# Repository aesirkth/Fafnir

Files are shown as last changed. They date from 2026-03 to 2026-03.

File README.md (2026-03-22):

# Fafnir
Propulsion Engine Controller

# Prerequisites
Follow [zephyr getting started guide](https://docs.zephyrproject.org/latest/develop/getting_started/index.html)

# Build 

```bash
cd zephyr-firmware
west update
cd fafnir
west build -b fafnir app --pristine
west flash
```

# Build for native simulation
```bash
docker run -ti -v /Volumes/external/zephyrproject/:/workdir -v /Volumes/external/aesir/Fafnir/zephyr-firmware/:/app ghcr.io/zephyrproject-rtos/zephyr-build:main
cd /app/fafnir
west build -b native_sim/native/64 app --pristine -- -DEXTRA_CONF_FILE=debug.conf
./build/zephyr/zephyr.exe
```
or
```bash
west build -b native_sim/native/64 app -- -DEXTRA_CONF_FILE=debug.conf && ./build/zephyr/zephyr.exe
```

## Using shell in simulation

You can send can messages like this
```bash
uart: ~$ can send can_loopback0 ID DATA
```

For example, running
```bash
uart: ~$ can send can_loopback0 123 0
```
will tell Fafnir to go into state STATE_INIT.

Running 
```bash
uart: ~$ can send can_loopback0 124 0 1
```
will use the override feature to set N2 Valve HIGH.

# CAN message specification to Fafnir

| CAN ID | byte | data | type  |
| --- | ---- | --- | ----- |
| 0x123  | 0 | launch sequence number (1-6) | uint8 | (setting states mode)
| 0x124  | 0 | Solenoid ID (1-4) | uint8 | (override mode)
| | 1 | 1 == open, 0 == closed | bool  |

Note that the launch sequence number corresponds to the launch sequence number as given in https://aesir.slab.com/posts/mjollnir-launch-sequence-2juh5ekp

Note that the Solenoid ID corresponds to the solenoid ports on the Fafnir board.
Mjollnir only has two solenoids which correspond to:
```
Solenoid ID 2 => Bypass valve
Solenoid ID 3 => Pilot valve
Solenoid ID 4 => Control vent
```
Solenoid IDs 1 and 4 are not connected and don't do anything.

## CAN acknowledges

| CAN ID | byte | data | meaning |
| --- | ---- | ---  | -----|
| 0x125  | 0 | 0x01 | Changing state! |
| | 1 |  \<byte\> |  the state we're changing to |
| 0x125  | 0 | 0x02 | Received valid override command! |
| | 1 | \<byte\> | The first byte we received  |
| | 2 |  \<byte\> | The second byte we received  |
| 0x125  | 0 | 0xF0 | Recieved invalid state |
| 0x125  | 0 | 0xF1 | Cannot perform ignition command while attempting ignition. (Protection against double send) |
|  | 1 | \<byte\> | State command we received |
| 0x125  | 0 | 0xF2 | Invalid state command |
| 0x125  | 0 | 0xF3 | Invalid override command |
| 0x125  | 0 | 0xF4 | Invalid pin given in override command |

The state we're changing to is of type equal to this C `enum`:
```c
typedef enum {
    STATE_IDLE,
    STATE_INIT,
    STATE_FILL,
    STATE_STOP_FILL,
    STATE_UMBILICAL,
    STATE_N2_PRESSURIZATION,
    STATE_IGNITION_1,
    STATE_IGNITION_2,
    STATE_IGNITION_3,
    STATE_IGNITION_4,
    STATE_SAFE,
    STATE_ABORT_BEFORE_COUNTDOWN,
    STATE_ABORT_AFTER_COUNTDOWN
} State_t;
```

Note that this is **NOT** the same as the launch sequence number used in the command above (0x123).

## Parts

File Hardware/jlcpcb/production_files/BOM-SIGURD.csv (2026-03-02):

Comment | Designator | Footprint | LCSC | Quantity
54.9k | R18 | R_0402_1005Metric | C11626 | 1
1k | R23,R24,R27,R28,R42 | R_0402_1005Metric | C11702 | 5
100p | C39 | C_0402_1005Metric | C1546 | 1
18p | C10,C9 | C_0402_1005Metric | C1549 | 2
47p | C26 | C_0402_1005Metric | C1567 | 1
30p | C34 | C_0402_1005Metric | C1570 | 1
1u | C38 | C_0603_1608Metric | C15849 | 1
10u | C29,C31,C43 | C_0805_2012Metric | C15850 | 3
3.9u | L1 | L_Changjiang_FNR4030S | C167872 | 1
49.9k | R17 | C_0402_1005Metric | C173335 | 1
3V | D10,D11,D14,D16,D18 | D_SOD-323 | C19077437 | 5
LED | D7 | D_0603_1608Metric | C19171301 | 1
10u | C13,C22,C41,C42 | C_0603_1608Metric | C194427 | 4
CSD17577Q3A | Q3 | VSON-8_3.3x3.3mm_P0.65mm_NexFET | C201632 | 1
MMBT3904 | Q1 | SOT-23 | C20526 | 1
1.0A | F10,F11,F7,F8,F9 | Fuse_1812_4532Metric | C20997 | 5
1k | R22,R4,R5 | R_0603_1608Metric | C21190 | 3
TPS56A37RPAR | IC3 | RPA0010A-MFG | C22392669 | 1
52.3k | R47 | R_0402_1005Metric | C227130 | 1
120 | R10 | R_0603_1608Metric_Pad0.98x0.95mm_HandSolder | C22787 | 1
rx | D4 | D_0603_1608Metric | C2286 | 1
LED | D9 | D_0603_1608Metric | C2288 | 1
LED | D21,D3 | D_0603_1608Metric | C2290 | 2
1M | R12,R13,R14,R15 | R_0603_1608Metric | C22935 | 4
3k | R30,R39 | R_0603_1608Metric | C22978 | 2
SZNUP2105L | D6 | SOT-23 | C23083861 | 1
470 | R2 | R_0603_1608Metric_Pad0.98x0.95mm_HandSolder | C23179 | 1
D | D2 | D_SOD-523 | C232841 | 1
4.7u | C1,C11,C2,C28 | C_0402_1005Metric | C23733 | 4
100 | R50 | R_0402_1005Metric | C25076 | 1
10 | R25,R51 | R_0402_1005Metric | C25077 | 2
120 | R52 | R_0402_1005Metric | C25079 | 1
10k | R11,R16,R20,R35,R45,R9 | R_0402_1005Metric | C25744 | 6
15k | R19,R46 | R_0402_1005Metric | C25756 | 2
20k | R49 | R_0402_1005Metric | C25765 | 1
10k | R3 | R_0603_1608Metric_Pad0.98x0.95mm_HandSolder | C25804 | 1
3.3k | R7,R8 | R_0402_1005Metric | C25890 | 2
INA226 | U4 | VSSOP-10_3x3mm_P0.5mm | C2653870 | 1
TCAN334GDCN | U1 | TSOT-23-8 | C2671013 | 1
ESD2CAN36DBZRQ1 | CR1,CR2 | SOT-23-3_DBZ_TEX | C284078 | 2
0.1u | C14,C15,C17,C19,C23,C27,C3,C30,C32,C35,C4,C40,C44,C5,C6,C7,C8 | C_0402_1005Metric | C307331 | 17
47k | R29,R31,R32,R33,R34,R36,R37,R38,R43,R44 | R_0603_1608Metric | C307918 | 10
~ | D12,D13,D15,D17,D19 | D_0603_1608Metric | C328933 | 5
24MHz | Y1 | Crystal_SMD_2016-4Pin_2.0x1.6mm | C37635323 | 1
~ | D1 | D_SOD-123 | C435489 | 1
7.5k | R26 | R_0603_1608Metric | C441926 | 1
VN7050ASTR | U7 | SOIC_050ASTR_STM | C443993 | 1
22u | C36,C37 | C_0805_2012Metric | C45783 | 2
383k | R48 | R_0402_1005Metric | C45993 | 1
TPS4H160AQPWPRQ1 | U6 | PWP0028C_N | C485918 | 1
0.02 | R21,R6 | R_2512_6332Metric | C49164694 | 2
10u | L2 | IND-SMD_L7.0-W6.6_FAUL06XX | C5298253 | 1
5.6u | L3 | IND-SMD_L6.6-W6.4 | C5378545 | 1
330n | C24 | C_0402_1005Metric | C5448882 | 1
22u | C16,C21 | C_0603_1608Metric | C59461 | 2
LM51231QRGRRQ1 | U3 | RGR0020C-MFG | C6286802 | 1
470p | C12 | C_0402_1005Metric | C76971 | 1
AP63203WU | U9 | TSOT-23-6 | C780769 | 1
CSD18543Q3A | Q4 | VSON-8_3.3x3.3mm_P0.65mm_NexFET | C840100 | 1
0.47u | C33 | C_0402_1005Metric | C92361 | 1
6.8n | C25 | C_0402_1005Metric | C93654 | 1
CMT-8504-100 | BZ1 | BUZ-SMD_4P-L7.5-W7.5-P7.59-TL | C95299 | 1
LED | D20 | D_0603_1608Metric | C965807 | 1

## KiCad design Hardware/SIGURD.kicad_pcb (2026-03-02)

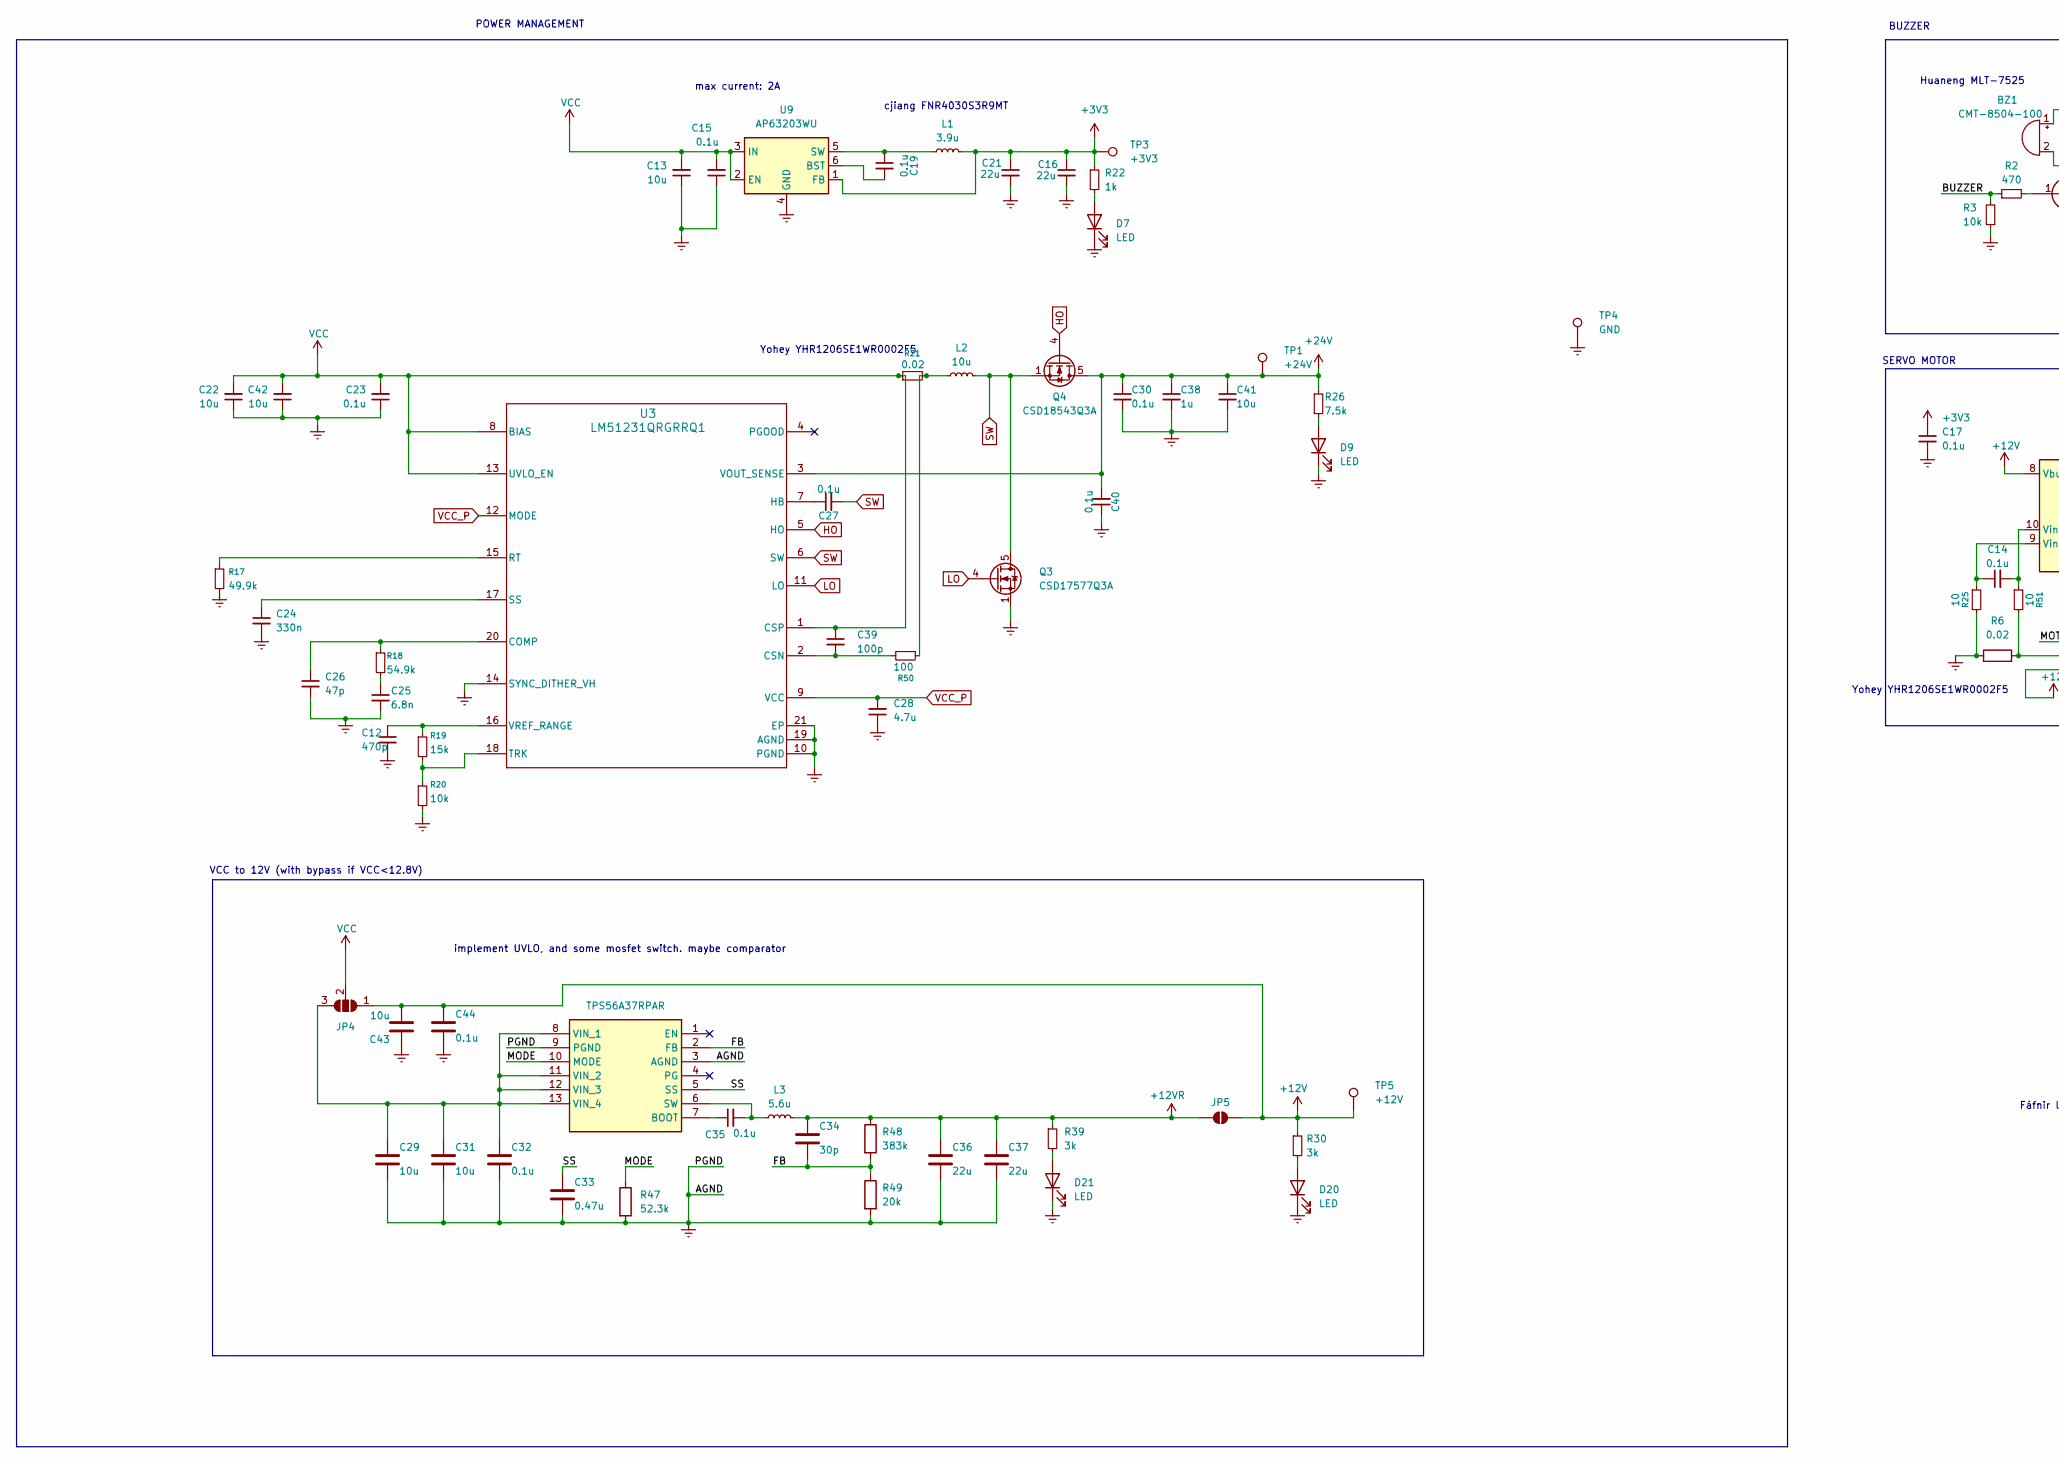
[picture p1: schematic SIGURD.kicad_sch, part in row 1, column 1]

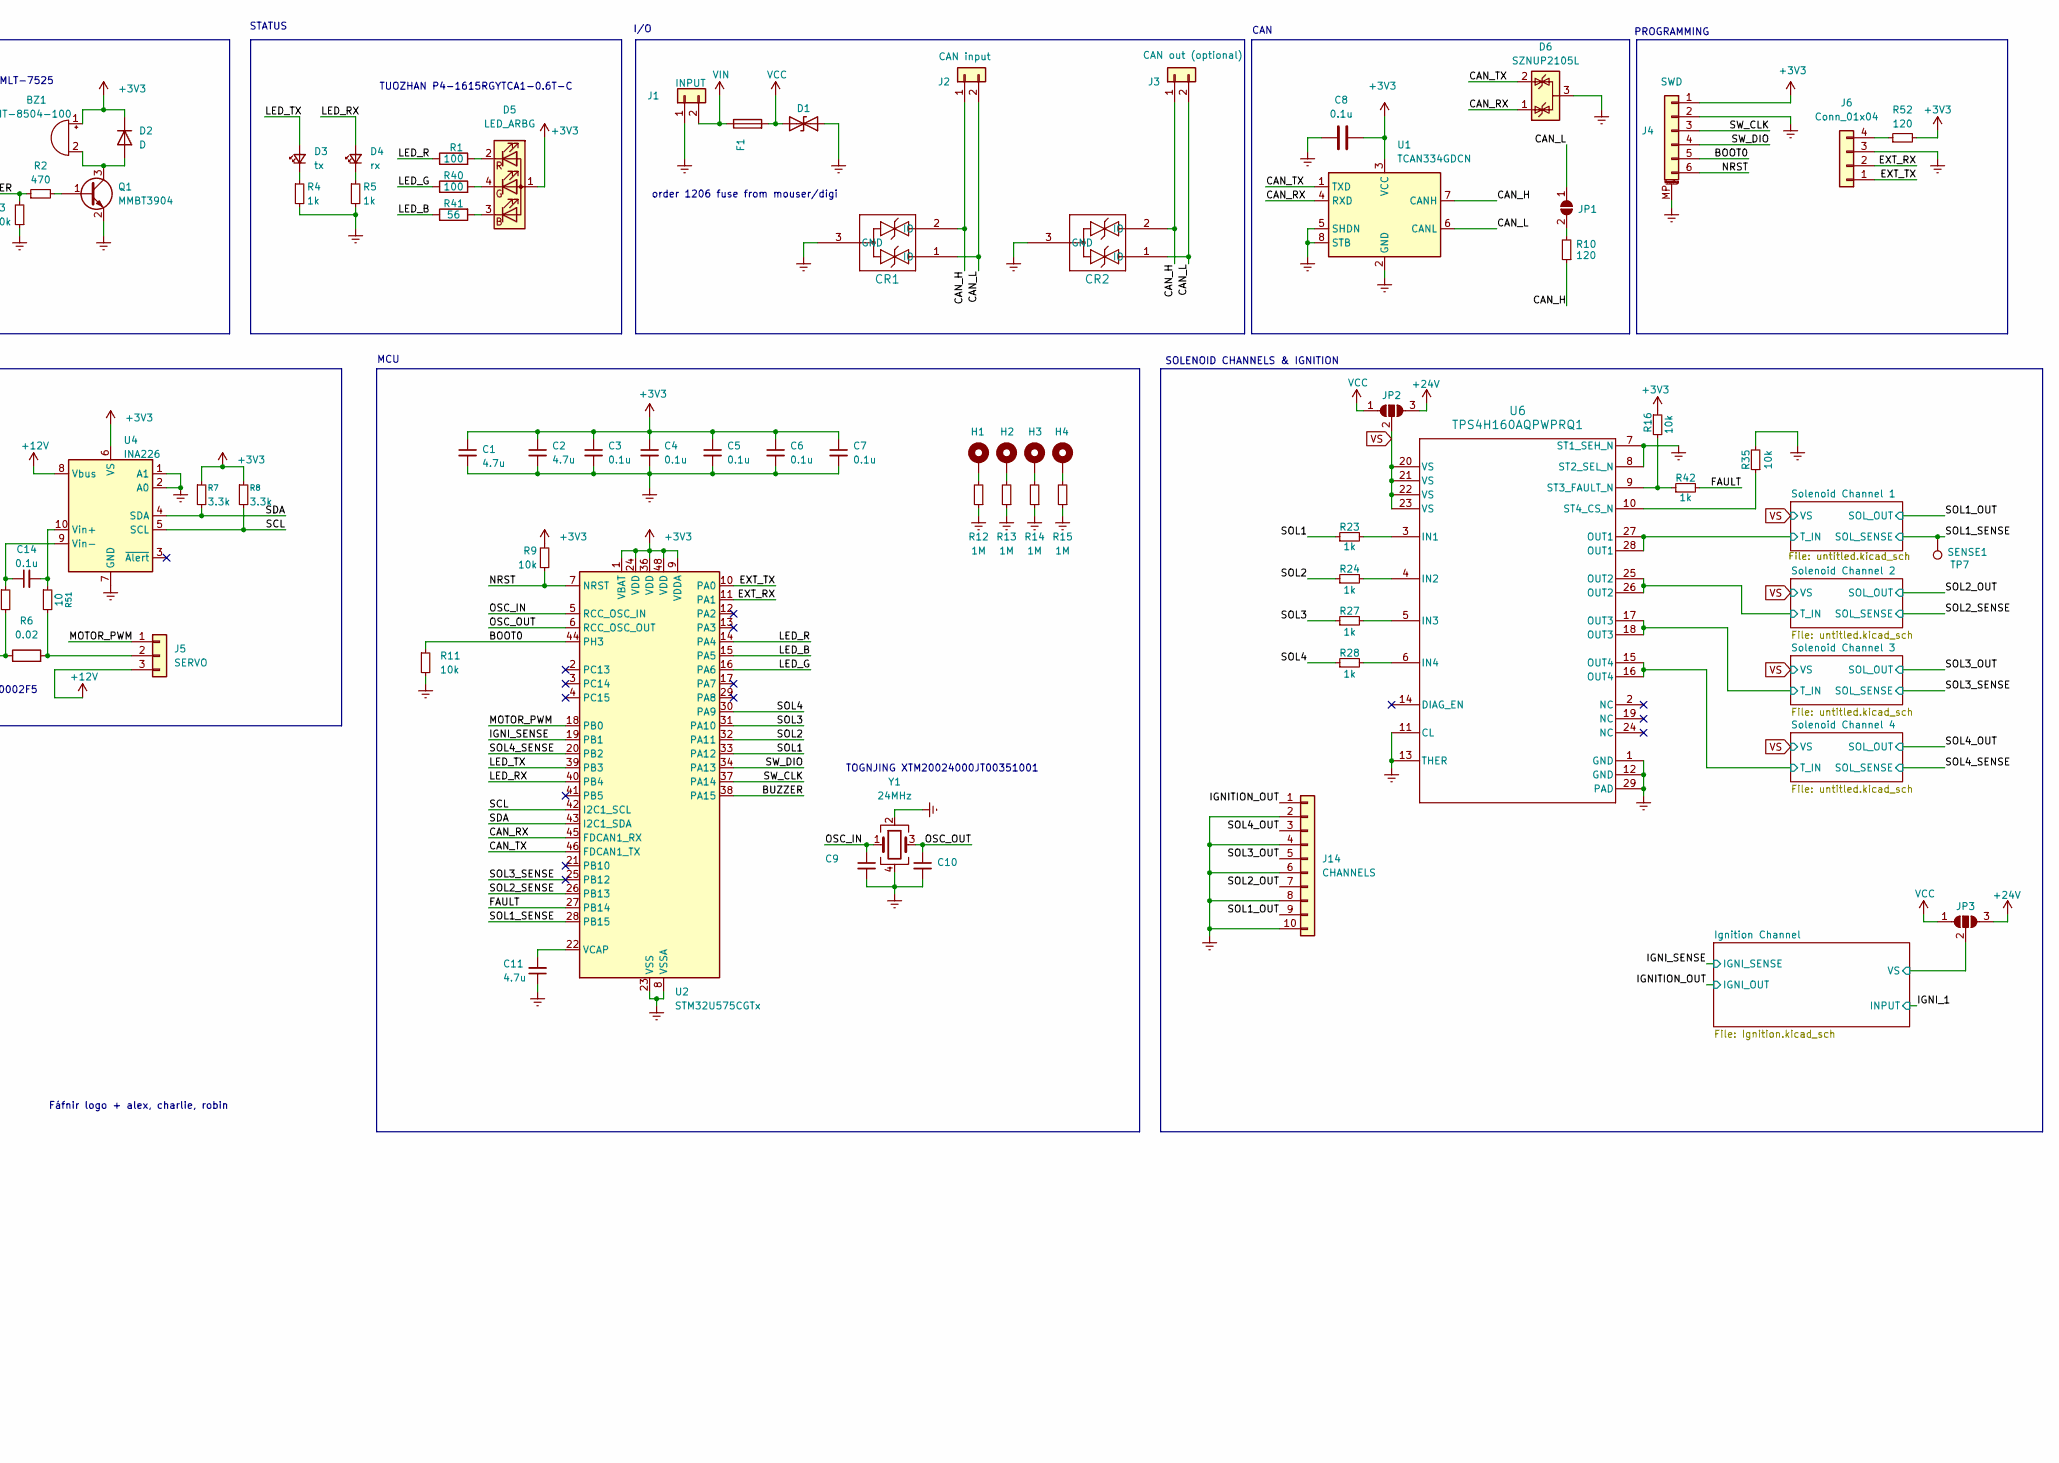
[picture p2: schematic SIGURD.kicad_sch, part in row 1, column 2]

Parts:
BZ1: CMT-8504-100; BUZ-SMD_4P-L7.5-W7.5-P7.59-TL
C1, C2, C11, C28: 4.7u; C_0402_1005Metric
C3, C4, C5, C6, C7, C8, C14, C15, C17, C19, C23, C27, C30, C32, C35, C40, C44: 0.1u; C_0402_1005Metric
C9, C10: 18p; C_0402_1005Metric
C12: 470p; C_0402_1005Metric
C13, C22, C41, C42: 10u; C_0603_1608Metric
C16, C21: 22u; C_0603_1608Metric
C24: 330n; C_0402_1005Metric
C25: 6.8n; C_0402_1005Metric
C26: 47p; C_0402_1005Metric
C29, C31, C43: 10u; C_0805_2012Metric
C33: 0.47u; C_0402_1005Metric
C34: 30p; C_0402_1005Metric
C36, C37: 22u; C_0805_2012Metric
C38: 1u; C_0603_1608Metric
C39: 100p; C_0402_1005Metric
CR1, CR2: ESD2CAN36DBZRQ1; SOT-23-3_DBZ_TEX
D1: D_SOD-123
D2: D; D_SOD-523
D3: tx; D_0603_1608Metric
D4: rx; D_0603_1608Metric
D5: LED_ARBG; LED_Lumex_SML-LX0404SIUPGUSB
D6: SZNUP2105L; SOT-23
D7, D9, D20, D21: LED; D_0603_1608Metric
F1: 15A; Fuse_1206_3216Metric
H1, H2, H3, H4: MountingHole_Pad; MountingHole_3.2mm_M3_Pad_Via
IC3: TPS56A37RPAR; RPA0010A-MFG; Mouser Part Number 595-TPS56A37RPAR
J1: INPUT; AMASS_XT30PW-F_1x02_P2.50mm_Horizontal
J2: CAN input; JST_XH_B2B-XH-A_1x02_P2.50mm_Vertical
J3: CAN out (optional); JST_XH_B2B-XH-A_1x02_P2.50mm_Vertical
J4: SWD; JST_SH_SM06B-SRSS-TB_1x06-1MP_P1.00mm_Horizontal
J5: SERVO; CONN_1727023_PXC
J6: Conn_01x04; PinSocket_1x04_P1.27mm_Vertical
J14: CHANNELS; CONN10_1935242_PXC
JP1: SolderJumper_2_Open; SolderJumper-2_P1.3mm_Open_TrianglePad1.0x1.5mm
JP2, JP3: SolderJumper_3_Open; SolderJumper-3_P2.0mm_Open_TrianglePad1.0x1.5mm_NumberLabels
JP4: SolderJumper_3_Open; SolderJumper-3_P1.3mm_Open_Pad1.0x1.5mm_NumberLabels
JP5: SolderJumper_2_Open; SolderJumper-2_P1.3mm_Open_Pad1.0x1.5mm
L1: 3.9u; L_Changjiang_FNR4030S
L2: 10u; IND-SMD_L7.0-W6.6_FAUL06XX
L3: 5.6u; IND-SMD_L6.6-W6.4
Q1: MMBT3904; SOT-23
Q3: CSD17577Q3A; VSON-8_3.3x3.3mm_P0.65mm_NexFET
Q4: CSD18543Q3A; VSON-8_3.3x3.3mm_P0.65mm_NexFET
R1, R40, R50: 100; R_0402_1005Metric
R2: 470; R_0603_1608Metric_Pad0.98x0.95mm_HandSolder
R3: 10k; R_0603_1608Metric_Pad0.98x0.95mm_HandSolder
R4, R5, R22: 1k; R_0603_1608Metric
R6, R21: 0.02; R_2512_6332Metric
R7, R8: 3.3k; R_0402_1005Metric
R9, R11, R16, R20, R35: 10k; R_0402_1005Metric
R10: 120; R_0603_1608Metric_Pad0.98x0.95mm_HandSolder
R12, R13, R14, R15: 1M; R_0603_1608Metric
R17: 49.9k; C_0402_1005Metric
R18: 54.9k; R_0402_1005Metric
R19: 15k; R_0402_1005Metric
R23, R24, R27, R28, R42: 1k; R_0402_1005Metric
R25, R51: 10; R_0402_1005Metric
R26: 7.5k; R_0603_1608Metric
R30, R39: 3k; R_0603_1608Metric
R41: 56; R_0402_1005Metric
R47: 52.3k; R_0402_1005Metric
R48: 383k; R_0402_1005Metric
R49: 20k; R_0402_1005Metric
R52: 120; R_0402_1005Metric
TP1: +24V; TestPoint_Pad_D2.0mm
TP3: +3V3; TestPoint_Pad_D2.0mm
TP4: GND; TestPoint_Pad_D2.0mm
TP5: +12V; TestPoint_Pad_D2.0mm
TP7: SENSE1; TestPoint_Pad_D2.0mm
U1: TCAN334GDCN; TSOT-23-8
U2: STM32U575CGTx; LQFP-48_7x7mm_P0.5mm
U3: LM51231QRGRRQ1; RGR0020C-MFG
U4: INA226; VSSOP-10_3x3mm_P0.5mm
U6: TPS4H160AQPWPRQ1; PWP0028C_N
U9: AP63203WU; TSOT-23-6
Y1: 24MHz; Crystal_SMD_2016-4Pin_2.0x1.6mm

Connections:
+3V3: BZ1.1 (-), C1.1, C2.1, C3.1, C4.1, C5.1, C6.1, C7.1, C8.2, C16.1, C17.1, C21.1, D2.1 (K), D5.1 (A), J4.1, L1.2, R7.1, R8.1, R9.2, R16.1, R22.1, R52.2, TP3.1, U1.3 (VCC), U2.1 (VBAT), U2.9 (VDDA), U2.24 (VDD), U2.36 (VDD), U2.48 (VDD), U4.6 (VS), U9.1 (FB)
+12V: C43.1, C44.2, J5.3, JP4.1 (A), JP5.2 (B), R30.1, TP5.1, U4.8 (Vbus)
+12VR: C34.2, C36.2, C37.2, JP5.1 (A), L3.2, R39.1, R48.1
+24V: C30.1, C38.1, C40.2, C41.1, JP2.3 (B), JP3.3 (B), Q4.5 (D), R26.1, TP1.1, U3.3 (VOUT_SENSE)
/BOOT0: J4.5, R11.1, U2.44 (PH3)
/BUZZER: R2.1, R3.2, U2.38 (PA15)
/CAN_H: CR1.2 (IO), CR2.2 (IO), J2.1, J3.1, R10.1, U1.7 (CANH)
/CAN_L: CR1.1 (IO), CR2.1 (IO), J2.2, J3.2, JP1.1 (A), U1.6 (CANL)
/CAN_RX: D6.1 (K), U1.4 (RXD), U2.45 (FDCAN1_RX)
/CAN_TX: D6.2 (K), U1.1 (TXD), U2.46 (FDCAN1_TX)
/EXT_RX: J6.2, U2.11 (PA1)
/EXT_TX: J6.1, U2.10 (PA0)
/FAULT: R42.2, U2.27 (PB14)
/FB: C34.1, IC3.2 (FB), R48.2, R49.1
/IGNITION_OUT: J14.1; also elsewhere on the board
/IGNI_SENSE: U2.19 (PB1); also elsewhere on the board
/Ignition Channel/VS: JP3.2 (C); also elsewhere on the board
/LED_B: R41.1, U2.15 (PA5)
/LED_G: R40.1, U2.16 (PA6)
/LED_R: R1.1, U2.14 (PA4)
/LED_RX: D4.2 (A), U2.40 (PB4)
/LED_TX: D3.2 (A), U2.39 (PB3)
/MODE: IC3.10 (MODE), R47.1
/MOTOR_PWM: J5.1, U2.18 (PB0)
/NRST: J4.6, R9.1, U2.7 (NRST)
/OSC_IN: C9.1, U2.5 (RCC_OSC_IN), Y1.1
/OSC_OUT: C10.1, U2.6 (RCC_OSC_OUT), Y1.3
/SCL: R8.2, U2.42 (I2C1_SCL), U4.5 (SCL)
/SDA: R7.2, U2.43 (I2C1_SDA), U4.4 (SDA)
/SOL1: R23.1, U2.33 (PA12)
/SOL1_OUT: J14.9; also elsewhere on the board
/SOL1_SENSE: TP7.1, U2.28 (PB15); also elsewhere on the board
/SOL2: R24.1, U2.32 (PA11)
/SOL2_OUT: J14.7; also elsewhere on the board
/SOL2_SENSE: U2.26 (PB13); also elsewhere on the board
/SOL3: R27.1, U2.31 (PA10)
/SOL3_OUT: J14.5; also elsewhere on the board
/SOL3_SENSE: U2.25 (PB12); also elsewhere on the board
/SOL4: R28.1, U2.30 (PA9)
/SOL4_OUT: J14.3; also elsewhere on the board
/SOL4_SENSE: U2.20 (PB2); also elsewhere on the board
/SS: C33.2, IC3.5 (SS)
/SW_CLK: J4.3, U2.37 (PA14)
/SW_DIO: J4.4, U2.34 (PA13)
/Solenoid Channel 1/T_IN: U6.27 (OUT1), U6.28 (OUT1); also elsewhere on the board
/Solenoid Channel 2/T_IN: U6.25 (OUT2), U6.26 (OUT2); also elsewhere on the board
/Solenoid Channel 3/T_IN: U6.17 (OUT3), U6.18 (OUT3); also elsewhere on the board
/Solenoid Channel 4/T_IN: U6.15 (OUT4), U6.16 (OUT4); also elsewhere on the board
Earth: C1.2, C2.2, C3.2, C4.2, C5.2, C6.2, C7.2, C8.1, C9.2, C10.2, C11.1, C12.2, C13.1, C15.1, C16.2, C17.2, C21.2, C22.1, C23.1, C24.2, C25.2, C26.2, C28.1, C29.1, C30.2, C31.1, C32.1, C33.1, C36.1, C37.1, C38.2, C40.1, C41.2, C42.1, C43.2, C44.1, CR1.3 (GND), CR2.3 (GND), D1.1 (A1), D6.3 (A), D7.1 (K), D9.1 (K), D20.1 (K), D21.1 (K), IC3.3 (AGND), IC3.9 (PGND), J1.1, J4.2, J4.MP (MountPin), J6.3, J14.2, J14.4, J14.6, J14.8, J14.10, Q1.2 (E), Q3.1 (S), Q3.2 (S), Q3.3 (S), R3.1, R4.2, R5.2, R6.1, R11.2, R12.1, R13.1, R14.1, R15.1, R17.2, R20.2, R25.2, R35.2, R47.2, R49.2, TP4.1, U1.2 (GND), U1.5 (SHDN), U1.8 (STB), U2.8 (VSSA), U2.23 (VSS), U2.35 (VSS), U2.47 (VSS), U3.10 (PGND), U3.14 (SYNC_DITHER_VH), U3.19 (AGND), U3.21 (EP), U3.22, U3.23, U3.24, U3.25, U3.26, U4.1 (A1), U4.2 (A0), U4.7 (GND), U6.1 (GND), U6.7 (ST1_SEH_N), U6.8 (ST2_SEL_N), U6.11 (CL), U6.12 (GND), U6.13 (THER), U6.29 (PAD), U6.V, U9.4 (GND), Y1.2, Y1.4; also elsewhere on the board
HO: Q4.4 (G), U3.5 (HO)
LO: Q3.4 (G), U3.11 (LO)
unnamed: BZ1.2 (+), D2.2 (A), Q1.3 (C)
unnamed: C25.1, R18.2
unnamed: D3.1 (K), R4.1
unnamed: D4.1 (K), R5.1
unnamed: D5.3 (BK), R41.2
unnamed: D5.4 (GK), R40.2
unnamed: D5.2 (RK), R1.2
unnamed: D7.2 (A), R22.2
unnamed: D9.2 (A), R26.2
unnamed: D20.2 (A), R30.2
unnamed: D21.2 (A), R39.2
unnamed: H1.1, R12.2
unnamed: H2.1, R13.2
unnamed: H3.1, R14.2
unnamed: H4.1, R15.2
unnamed: C35.1, IC3.7 (BOOT)
unnamed: C35.2, IC3.6 (SW), L3.1
unnamed: C29.2, C31.2, C32.2, IC3.8 (VIN_1), IC3.11 (VIN_2), IC3.12 (VIN_3), IC3.13 (VIN_4), JP4.3 (B)
unnamed: J5.2, R6.2, R51.2
unnamed: J6.4, R52.1
unnamed: JP1.2 (B), R10.2
unnamed: L2.1, R21.2, R50.1
unnamed: Q1.1 (B), R2.2
unnamed: C11.2, U2.22 (VCAP)
unnamed: C26.1, R18.1, U3.20 (COMP)
unnamed: C39.2, R50.2, U3.2 (CSN)
unnamed: C27.1, U3.7 (HB)
unnamed: R17.1, U3.15 (RT)
unnamed: C24.1, U3.17 (SS)
unnamed: R19.2, R20.1, U3.18 (TRK)
unnamed: C12.1, R19.1, U3.16 (VREF_RANGE)
unnamed: C14.2, R51.1, U4.10 (Vin+)
unnamed: C14.1, R25.1, U4.9 (Vin-)
unnamed: R23.2, U6.3 (IN1)
unnamed: R24.2, U6.4 (IN2)
unnamed: R27.2, U6.5 (IN3)
unnamed: R28.2, U6.6 (IN4)
unnamed: R16.2, R42.1, U6.9 (ST3_FAULT_N)
unnamed: R35.1, U6.10 (ST4_CS_N)
unnamed: C19.2, U9.6 (BST)
unnamed: C19.1, L1.1, U9.5 (SW)
SW: C27.2, L2.2, Q3.5 (D), Q4.1 (S), Q4.2 (S), Q4.3 (S), U3.6 (SW)
VCC: C13.2, C15.2, C22.2, C23.2, C39.1, C42.2, D1.2 (A2), F1.2, JP2.1 (A), JP3.1 (A), JP4.2 (C), R21.1, U3.1 (CSP), U3.8 (BIAS), U3.13 (UVLO_EN), U9.2 (EN), U9.3 (IN)
VCC_P: C28.2, U3.9 (VCC), U3.12 (MODE)
VIN: F1.1, J1.2
VS: JP2.2 (C), U6.20 (VS), U6.21 (VS), U6.22 (VS), U6.23 (VS); also elsewhere on the board

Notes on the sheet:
BUZZER
VCC to 12V (with bypass if VCC<12.8V)
I/O
SOLENOID CHANNELS & IGNITION
Yohey YHR1206SE1WR0002F5
Huaneng MLT-7525
Fáfnir logo + alex, charlie, robin
PROGRAMMING
cjiang FNR4030S3R9MT
max current: 2A
implement UVLO, and some mosfet switch. maybe comparator
order 1206 fuse from mouser/digi
CAN
POWER MANAGEMENT
TOGNJING XTM20024000JT00351001
SERVO MOTOR
TUOZHAN P4-1615RGYTCA1-0.6T-C
MCU
STATUS

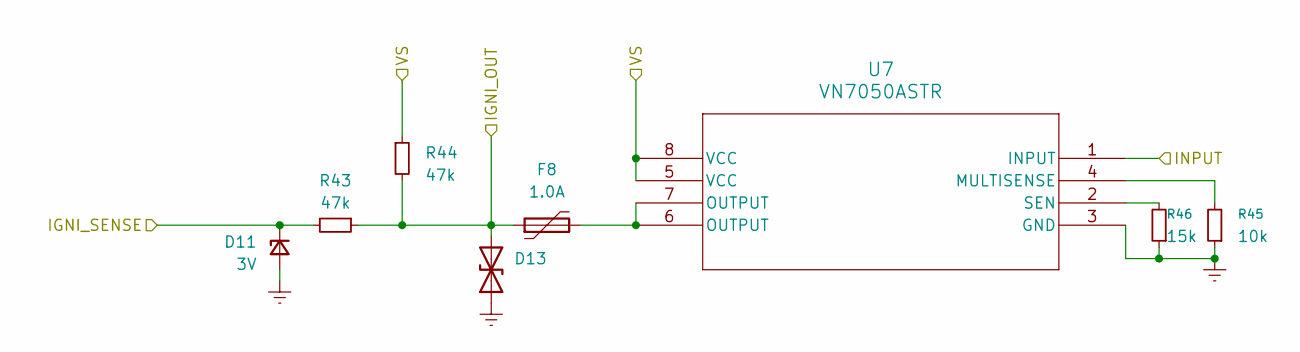
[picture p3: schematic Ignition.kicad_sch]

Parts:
D11: 3V; D_SOD-323
D13: D_0603_1608Metric
F8: 1.0A; Fuse_1812_4532Metric
R43, R44: 47k; R_0603_1608Metric
R45: 10k; R_0402_1005Metric
R46: 15k; R_0402_1005Metric
U7: VN7050ASTR; SOIC_050ASTR_STM

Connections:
/IGNITION_OUT: D13.2 (A2), F8.1, R43.1, R44.2; also elsewhere on the board
/IGNI_1: U7.1 (INPUT)
/IGNI_SENSE: D11.1 (K), R43.2; also elsewhere on the board
/Ignition Channel/VS: R44.1, U7.5 (VCC), U7.8 (VCC); also elsewhere on the board
Earth: D11.2 (A), D13.1 (A1), R45.1, R46.1, U7.3 (GND); also elsewhere on the board
unnamed: F8.2, U7.6 (OUTPUT), U7.7 (OUTPUT)
unnamed: R45.2, U7.4 (MULTISENSE)
unnamed: R46.2, U7.2 (SEN)

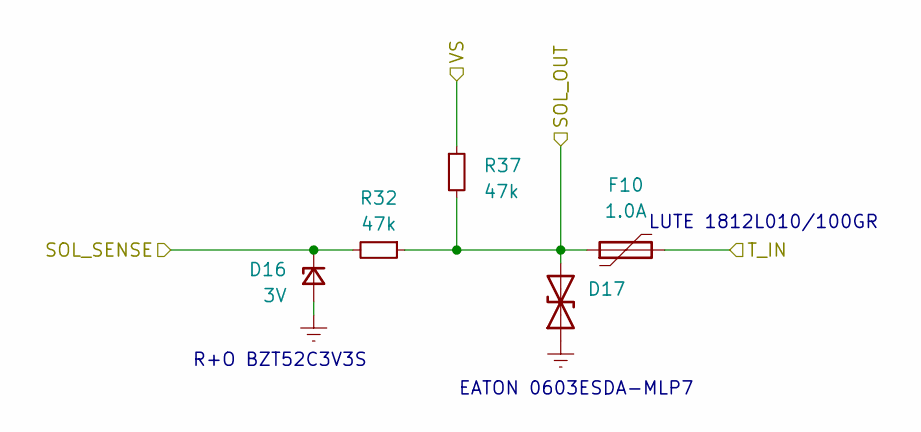
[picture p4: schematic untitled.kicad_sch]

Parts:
D16: 3V; D_SOD-323
D17: D_0603_1608Metric
F10: 1.0A; Fuse_1812_4532Metric
R32, R37: 47k; R_0603_1608Metric

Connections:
/SOL3_OUT: D17.2 (A2), F10.1, R32.1, R37.2; also elsewhere on the board
/SOL3_SENSE: D16.1 (K), R32.2; also elsewhere on the board
/Solenoid Channel 3/T_IN: F10.2; also elsewhere on the board
Earth: D16.2 (A), D17.1 (A1); also elsewhere on the board
VS: R37.1; also elsewhere on the board

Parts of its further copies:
D10, D14, D18: 3V; D_SOD-323
D12, D15, D19: D_0603_1608Metric
F7, F9, F11: 1.0A; Fuse_1812_4532Metric
R29, R31, R33, R34, R36, R38: 47k; R_0603_1608Metric

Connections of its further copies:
/SOL1_OUT: D12.2 (A2), F7.1, R29.1, R34.2; also elsewhere on the board
/SOL1_SENSE: D10.1 (K), R29.2; also elsewhere on the board
/SOL2_OUT: D15.2 (A2), F9.1, R31.1, R36.2; also elsewhere on the board
/SOL2_SENSE: D14.1 (K), R31.2; also elsewhere on the board
/SOL4_OUT: D19.2 (A2), F11.1, R33.1, R38.2; also elsewhere on the board
/SOL4_SENSE: D18.1 (K), R33.2; also elsewhere on the board
/Solenoid Channel 1/T_IN: F7.2; also elsewhere on the board
/Solenoid Channel 2/T_IN: F9.2; also elsewhere on the board
/Solenoid Channel 4/T_IN: F11.2; also elsewhere on the board
Earth: D10.2 (A), D12.1 (A1), D14.2 (A), D15.1 (A1), D18.2 (A), D19.1 (A1); also elsewhere on the board
VS: R34.1, R36.1, R38.1; also elsewhere on the board

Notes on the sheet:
R+O BZT52C3V3S
LUTE 1812L010/100GR
EATON 0603ESDA-MLP7

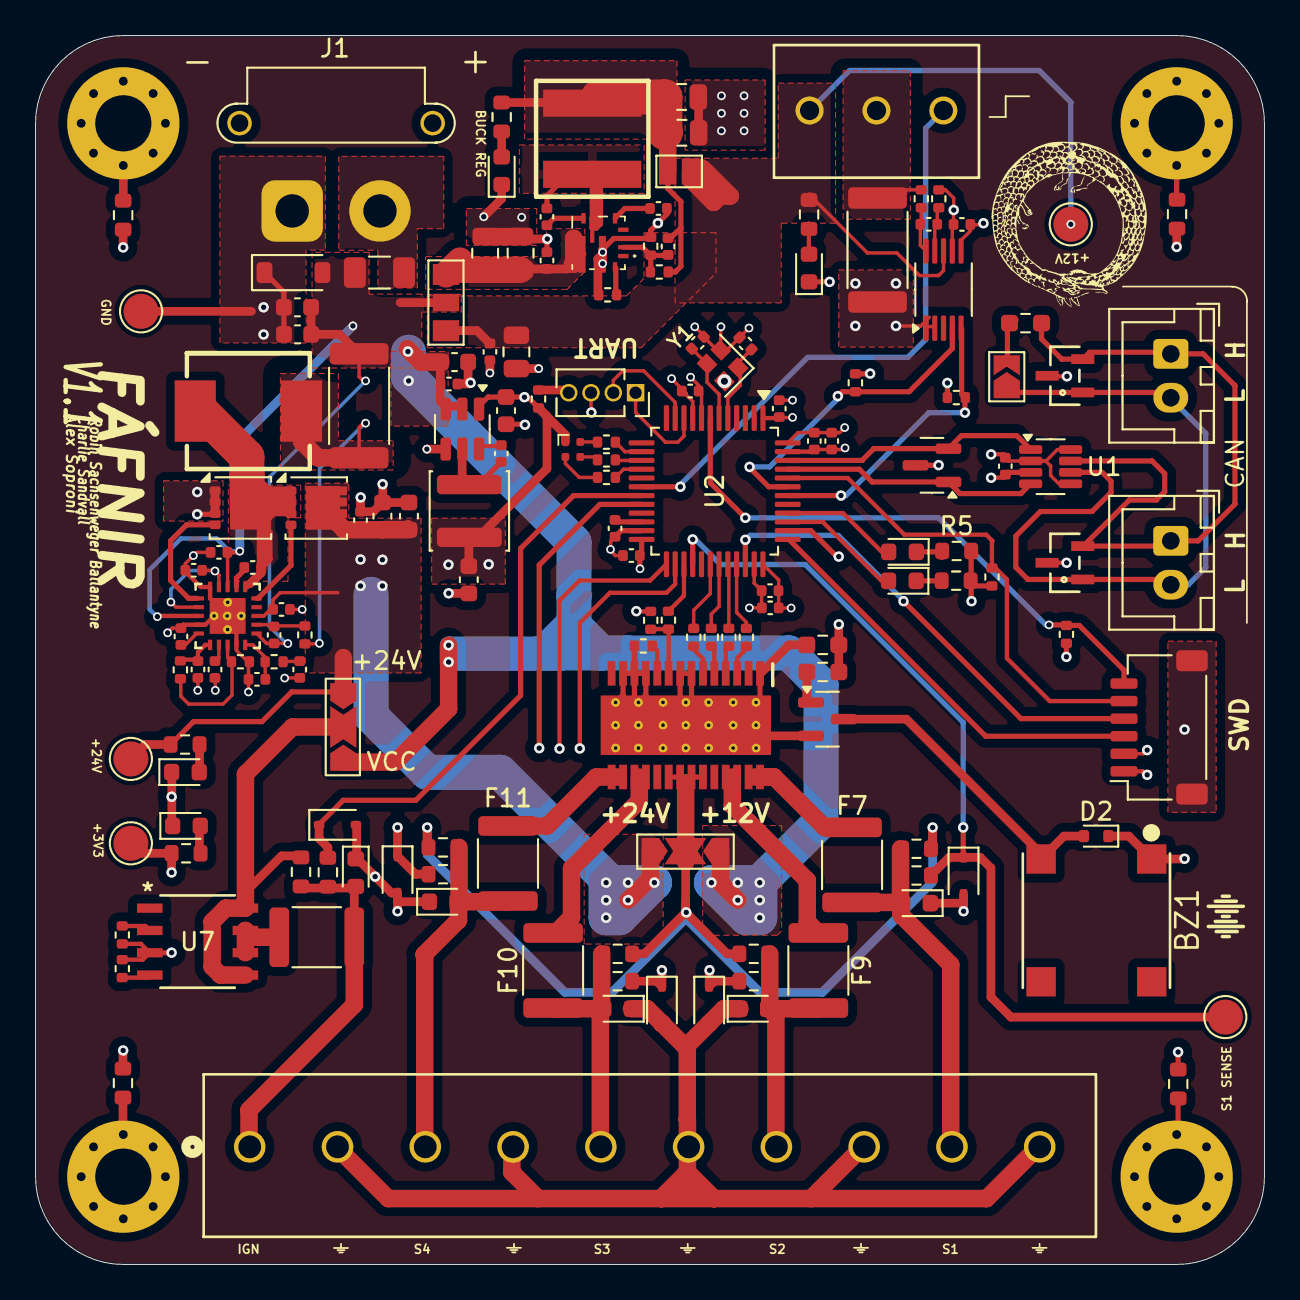
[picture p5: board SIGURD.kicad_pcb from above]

Board: 4 copper layers, 70.0 x 70.0 mm, 159 parts (0 on the bottom side), 100 nets.

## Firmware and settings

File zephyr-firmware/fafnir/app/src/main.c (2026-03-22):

/*
 * Copyright (c) 2016 Intel Corporation
 *
 * SPDX-License-Identifier: Apache-2.0
 */

#include "can_com.h"

#if defined(CONFIG_BOARD_NATIVE_SIM) 
#include "gpio_emul_shell.h"
#endif

#include "main.h"

#include <zephyr/logging/log.h>
#include <zephyr/kernel.h>
#include <zephyr/drivers/gpio.h>
#include <zephyr/drivers/pwm.h>



/* 1000 msec = 1 sec */
#define SLEEP_TIME_MS   4000


LOG_MODULE_REGISTER(main_func);

static const struct gpio_dt_spec led = GPIO_DT_SPEC_GET(DT_ALIAS(rxled), gpios);

// Disable servo pwm if using board Native Sim 
// #if !defined(CONFIG_BOARD_NATIVE_SIM) 
// static const struct pwm_dt_spec pwm_servo = PWM_DT_SPEC_GET(DT_NODELABEL(servo));
// #define SERVO_PERIOD PWM_MSEC(20)
// #endif

#if !defined(CONFIG_BOARD_NATIVE_SIM) 
static const struct pwm_dt_spec pwm_servo = PWM_DT_SPEC_GET(DT_ALIAS(servo));
#define SERVO_PERIOD PWM_MSEC(20)
#endif

static const struct gpio_dt_spec N2_valve = GPIO_DT_SPEC_GET(DT_ALIAS(n2valve), gpios);
static const struct gpio_dt_spec vent_valve = GPIO_DT_SPEC_GET(DT_ALIAS(ventvalve), gpios);
static const struct gpio_dt_spec abort_valve = GPIO_DT_SPEC_GET(DT_ALIAS(abortvalve), gpios);
static const struct gpio_dt_spec extra_valve = GPIO_DT_SPEC_GET(DT_ALIAS(extravalve), gpios);

// static const struct gpio_dt_spec N2_sense = GPIO_DT_SPEC_GET(DT_ALIAS(n2sense), gpios);
// static const struct gpio_dt_spec vent_sense = GPIO_DT_SPEC_GET(DT_ALIAS(ventsense), gpios);
// static const struct gpio_dt_spec main_sense = GPIO_DT_SPEC_GET(DT_ALIAS(mainsense), gpios);
// static const struct gpio_dt_spec abort_sense = GPIO_DT_SPEC_GET(DT_ALIAS(abortsense), gpios);
// static const struct gpio_dt_spec ignition_sense = GPIO_DT_SPEC_GET(DT_ALIAS(ignitionsense), gpios);

#define NUM_CHANNELS 4
// const struct gpio_dt_spec solenoidSense[NUM_CHANNELS] = {N2_sense, vent_sense, abort_sense, ignition_sense};
const struct gpio_dt_spec pyroPins[NUM_CHANNELS] = {N2_valve, vent_valve, abort_valve, extra_valve};


typedef enum {
    STATE_IDLE,
    STATE_INIT,
    STATE_FILL,
    STATE_STOP_FILL,
    STATE_UMBILICAL,
    STATE_N2_PRESSURIZATION,
    STATE_IGNITION_1,
    STATE_IGNITION_2,
    STATE_IGNITION_3,
    STATE_IGNITION_4,
    STATE_SAFE,
    STATE_ABORT_BEFORE_COUNTDOWN,
    STATE_ABORT_AFTER_COUNTDOWN
} State_t;

State_t systemState = STATE_IDLE;
bool trigger = true;

bool isStateBeforeCountdown(State_t state) {
    switch (state) {
    case STATE_IDLE:
        return true;
    case STATE_INIT:
        return true;
    case STATE_FILL:
        return true;
    case STATE_STOP_FILL:
        return true;
    case STATE_UMBILICAL:
        return true;
    case STATE_N2_PRESSURIZATION:
        return true;
    case STATE_IGNITION_1:
        return true;
    case STATE_IGNITION_2:
        return true;
    case STATE_IGNITION_3:
        return false; // Double checked with xiao
    case STATE_IGNITION_4:
        return false;
    case STATE_SAFE:
        return false;
    case STATE_ABORT_BEFORE_COUNTDOWN:
        return false;
    case STATE_ABORT_AFTER_COUNTDOWN:
        return false;
    }
    LOG_ERR("Invalid state passed!");
    return true;
}

bool isStateIgnition(State_t state) {
    switch (state) {
    case STATE_IDLE:
        return false;
    case STATE_INIT:
        return false;
    case STATE_FILL:
        return false;
    case STATE_STOP_FILL:
        return false;
    case STATE_UMBILICAL:
        return false;
    case STATE_N2_PRESSURIZATION:
        return false;
    case STATE_IGNITION_1:
        return true;
    case STATE_IGNITION_2:
        return true;
    case STATE_IGNITION_3:
        return true;
    case STATE_IGNITION_4:
        return true;
    case STATE_SAFE:
        return false;
    case STATE_ABORT_BEFORE_COUNTDOWN:
        return false;
    case STATE_ABORT_AFTER_COUNTDOWN:
        return false;
    }
    LOG_ERR("Invalid state passed!");
    return false;
}


/* 
 * A CAN message with `data`, is interpreted as a command meaning:
 * "Change your state to `state_can_id_map[data]`".
*/
State_t state_can_id_map[] = {
    STATE_INIT,
    STATE_FILL,
    STATE_STOP_FILL,
    STATE_UMBILICAL,
    STATE_N2_PRESSURIZATION,
    STATE_IGNITION_1,
    STATE_SAFE,
    STATE_ABORT_BEFORE_COUNTDOWN // Used for any abort message, not just before countdown.
};

void changeStateToIgnition2_cb() { 
    if(systemState != STATE_IGNITION_1) return;

    systemState = STATE_IGNITION_2;
    LOG_INF("changeStateToIgnition2_cb triggered going into STATE_IGNITION_2!");
    trigger = true;
}

void changeStateToIgnition3_cb() { 
    if(systemState != STATE_IGNITION_2) return;

    systemState = STATE_IGNITION_3;
    LOG_INF("changeStateToIgnition3_cb triggered going into STATE_IGNITION_3!");
    trigger = true;
}

void changeStateToIgnition4_cb() { 
    if(systemState != STATE_IGNITION_3) return;

    systemState = STATE_IGNITION_4;
    LOG_INF("changeStateToIgnition4_cb triggered going into STATE_IGNITION_4!");
    trigger = true;
}

void changeStateToSafeing_cb() { 
    if(systemState != STATE_IGNITION_4) return;

    systemState = STATE_SAFE;
    LOG_INF("changeStateToSafeing_cb triggered going into STATE_SAFE!");
    trigger = true;
}

// uint8_t pyroSense(uint8_t index) {
// 	if (index >= NUM_PYROS) return 69; //69 means error
//     //HIGH = continuity detected (return 1)
//     //LOW = open circuit (return 0)

// 	int state = gpio_pin_get_dt(&solenoidSense[index]);

//     return state;
// }

void servoZero(void) {
	servoRotate(0.0f);
}

void servoRotate(float angle) {
	//The angle is mapped to -135 to 135 to properly represent CW and CCW rotations
	//Input of +90 == 90 deg rotation CW from the zero position.
    LOG_INF("setting angle of pwm_servo = %d\n", (int) angle);

    #if !defined(CONFIG_BOARD_NATIVE_SIM)
    {
        if (angle < -135 || angle > 135) return;
        angle = 135.0f + angle; //135 degrees is the zero/middle position, since the servo motor can rotate 270 deg

        float degRatio = angle / 270.0f;

        float duty = degRatio * 0.10f + 0.025f;  //mapping to 2.5%–12.5% duty cycle

        pwm_set_dt(&pwm_servo, SERVO_PERIOD, (uint32_t) SERVO_PERIOD*duty); // move it a bit
    }
    #endif
}

void set_pin(const struct gpio_dt_spec *pin, bool value) {
    LOG_INF("PIN[%d] set to value %d", pin->pin, value);
    gpio_pin_set_dt(pin, value);
}


const struct can_filter filter = {
    .flags = 0,
    .id = 0x123,
    .mask = 0b11111111111 
};
void can_rx_cb(const struct device *const device, struct can_frame *frame, void *user_data) {

    if (frame->dlc != 1) {
        LOG_ERR("received packet with id %d has length %d. Fafnir expects all packets to have size 1.", frame->id, frame->dlc);
        uint8_t data[1] = {0xF2}; // Incorrect message format
        submit_can_pkt(data, 1);
        return;
    }

    // if(systemState == STATE_ABORT_BEFORE_COUNTDOWN || systemState == STATE_ABORT_AFTER_COUNTDOWN) {
    //     LOG_ERR("CAN message recieved but ignored because system is aborted.");
    //     return;
    // }


    size_t message_data = frame->data[0];

    if (!(0 <= message_data && message_data <= 7)) {
        uint8_t data[1] = {0xF0}; // Incorrect state
        submit_can_pkt(data, 1);
        return;
    }
    State_t message_state = state_can_id_map[message_data];


    if (isStateIgnition(systemState) && message_state == STATE_IGNITION_1) {
        uint8_t data[2] = {0xF1, frame->data[0]}; // Cannot perform ignition command while in ignition state.
        submit_can_pkt(data, 2);
        return;
    }

    if (message_state == STATE_ABORT_BEFORE_COUNTDOWN) { // STATE_ABORT_BEFORE_COUNTDOWN represents any abort
        if(isStateBeforeCountdown(systemState)) {
            systemState = STATE_ABORT_BEFORE_COUNTDOWN;
        } else {
            systemState = STATE_ABORT_AFTER_COUNTDOWN;
        }
    } else {
        systemState = state_can_id_map[message_data];
    }

    LOG_INF("Recieved CAN message rx: %#X: frame->dlc: %d. Switching state to %d", frame->id, frame->dlc, systemState);

    trigger = true;

}

const struct can_filter override_filter = {
    .flags = 0,
    .id = 0x124,
    .mask = 0b11111111111 
};
void can_rx_override_cb(const struct device *const device, struct can_frame *frame, void *user_data) {

    if (frame->dlc != 2) {
        LOG_ERR("received packet with id %d has length %d. Override requires 2 arguments PIN, VALUE.", frame->id, frame->dlc);
        uint8_t data[1] = {0xF3}; // Incorrect override message format!
        submit_can_pkt(data, 1);
        return;
    }
    size_t pin = frame->data[0];
    size_t value = frame->data[1];

    LOG_INF("Recieved CAN message rx: %#X: frame->dlc: %d. Setting pin[%d] := %d", frame->id, frame->dlc, pin, value);
    switch (pin) {
    case 0:
        int8_t signed_value = (int8_t) value;
        servoRotate(90.0 * ((double) signed_value/127.0) );
        break;
    case 1:
        set_pin(&extra_valve, value);
        break;
    case 2:
        set_pin(&abort_valve, value);
        break;
    case 3:
        set_pin(&vent_valve, value);
        break;
    case 4:
        set_pin(&N2_valve, value);
        break;
    default:
        LOG_ERR("Invalid pin!");
        uint8_t data[3] = {0xF4, frame->data[0], frame->data[1]}; // Incorrect pin!
        submit_can_pkt(data, 3);
        return;
        break;
    }
    LOG_ERR("Invalid pin!");
    uint8_t data[3] = {0x02, frame->data[0], frame->data[1]}; // Succesffuly received override command
    submit_can_pkt(data, 3);
}

static uint8_t data[2];


void configure_output_pin(const struct gpio_dt_spec *pin) {
	int ret;
    int ready = gpio_is_ready_dt(pin);
    if (!ready) {
        LOG_ERR("pin not ready");
        return;
    }

    ret = gpio_pin_configure_dt(pin, GPIO_OUTPUT);

    if (ret < 0) {
        LOG_ERR("pin configure failed %d", ret);
        return;
    }
}

void configure_input_pin(const struct gpio_dt_spec *pin) {
	int ret;
    int ready = gpio_is_ready_dt(pin);
    if (!ready) {
        LOG_ERR("pin not ready");
        return;
    }

    ret = gpio_pin_configure_dt(pin, GPIO_INPUT);
    if (ret < 0) {
        LOG_ERR("pin configure failed %d", ret);
        return;
    }
}

K_TIMER_DEFINE(TMinus7_timer, changeStateToIgnition2_cb, NULL);
K_TIMER_DEFINE(TMinus2_timer, changeStateToIgnition3_cb, NULL);
K_TIMER_DEFINE(TMinus0_timer, changeStateToIgnition4_cb, NULL);
K_TIMER_DEFINE(TPlus30_timer, changeStateToSafeing_cb, NULL);

void evaluateState() { 
    LOG_INF("Evaluating state: %d", systemState);
    uint8_t data[2] = {0x01, systemState};
    submit_can_pkt(data, 2); // Changing state acknowledge!
    switch(systemState) {
        case STATE_IDLE:
            set_pin(&N2_valve, 0);
            set_pin(&vent_valve, 0);
            set_pin(&abort_valve, 0);
            servoZero(); // Close Main Valve TODO: Is this correct? 
            set_pin(&led, 0);
        break;
        case STATE_INIT:
            set_pin(&N2_valve, 0);
            set_pin(&vent_valve, 1);
            set_pin(&abort_valve, 0);
            servoZero();
            set_pin(&led, 0);
        break;
        case STATE_FILL:
            // Same as STATE_INIT
            set_pin(&N2_valve, 0);
            set_pin(&vent_valve, 1);
            set_pin(&abort_valve, 0);
            servoZero();
            set_pin(&led, 0);
        break;

        case STATE_STOP_FILL:
            set_pin(&N2_valve, 0);
            set_pin(&vent_valve, 0);
            set_pin(&abort_valve, 0);
            servoZero();
            set_pin(&led, 0);
        break;

        case STATE_UMBILICAL:
            // Same as STATE_STOP_FILL
            set_pin(&N2_valve, 0);
            set_pin(&vent_valve, 0);
            set_pin(&abort_valve, 0);
            servoZero();
            set_pin(&led, 0);
        break;

        case STATE_N2_PRESSURIZATION:
            set_pin(&N2_valve, 1);
            set_pin(&vent_valve, 0);
            set_pin(&abort_valve, 0);
            servoZero();
            set_pin(&led, 0);
        break;

        case STATE_IGNITION_1:
            set_pin(&N2_valve, 1);
            set_pin(&vent_valve, 0);
            set_pin(&abort_valve, 0);
            servoZero();
            set_pin(&led, 1);
            // TODO: Buzzer
            // TODO: Are the times correct? Maybe confused about T-10, T-7, etc...
            // It is now T-10, 3000ms until T-7.
            k_timer_start(&TMinus7_timer, K_MSEC(3000), K_NO_WAIT);
        break;

        case STATE_IGNITION_2: 
            set_pin(&N2_valve, 1);
            set_pin(&vent_valve, 0);
            set_pin(&abort_valve, 0);
            servoZero();
            set_pin(&led, 1);
            // It is now T-7, 5000ms until T-2.
            k_timer_start(&TMinus2_timer, K_MSEC(5000), K_NO_WAIT);
        break;

        case STATE_IGNITION_3:
            set_pin(&N2_valve, 1);
            set_pin(&vent_valve, 0);
            set_pin(&abort_valve, 0);
            servoRotate(30.0); // TODO: What angle is 10%?
            set_pin(&led, 1);
            // It is now T-2, 2000ms until T-0.
            k_timer_start(&TMinus0_timer, K_MSEC(2000), K_NO_WAIT);
            
        break;

        case STATE_IGNITION_4:
            set_pin(&N2_valve, 1);
            set_pin(&vent_valve, 0);
            set_pin(&abort_valve, 0);
            servoRotate(1.0 * 90.0); // TODO: What angle is 100%?
            set_pin(&led, 1);
            // It is now T-0, T+30 in 30000 ms
            k_timer_start(&TPlus30_timer, K_MSEC(30000), K_NO_WAIT);
        break;

        case STATE_SAFE:
            set_pin(&N2_valve, 1);
            set_pin(&vent_valve, 1);
            set_pin(&abort_valve, 1);
            servoRotate(1.0 * 90.0);
            set_pin(&led, 1);
        break;

        case STATE_ABORT_BEFORE_COUNTDOWN:
            set_pin(&N2_valve, 1);
            set_pin(&vent_valve, 1);
            set_pin(&abort_valve, 1);
            servoZero();
            set_pin(&led, 1);
        break;

        case STATE_ABORT_AFTER_COUNTDOWN:
            set_pin(&N2_valve, 1);
            set_pin(&vent_valve, 1);
            set_pin(&abort_valve, 1);
            servoRotate(1.0 * 90.0);
            set_pin(&led, 1);
        break;

    }

    // TODO: What should we do if the sensing pins report no continuity?
    // TODO: Send back response CAN messages? What should they say?
}


int main(void)
{
	int ret;


    #if !defined(CONFIG_BOARD_NATIVE_SIM) 
	if (!pwm_is_ready_dt(&pwm_servo)) {
		printk("Error: PWM device %s is not ready\n",
		       pwm_servo.dev->name);
		return 0;
	}
    #endif

    init_can();
    add_filter_can(can_rx_cb, filter, NULL);
    add_filter_can(can_rx_override_cb, override_filter, NULL);



    // data[0] = 39;
    // data[1] = 59;
    // submit_can_pkt(data, 2);

    configure_output_pin(&led);

    for (size_t i = 0; i < NUM_CHANNELS; i++) {
        configure_output_pin(&pyroPins[i]);
        // configure_input_pin(&solenoidSense[i]);
    }

    
	while (1) {
		// ret = gpio_pin_toggle_dt(&led);
		// uint8_t senseState = pyroSense(0);

        if(trigger) {
            evaluateState();
            trigger = false;
        }

        // uint8_t data[3] = {2, 3, 4};
        // submit_can_pkt(data, 3);
		k_msleep(10);
	}
	return 0;
}

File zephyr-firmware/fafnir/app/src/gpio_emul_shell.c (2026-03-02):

#if defined(CONFIG_BOARD_NATIVE_SIM) 
#include "gpio_emul_shell.h"
#include <zephyr/shell/shell.h>
#include <zephyr/drivers/gpio/gpio_emul.h>
#include <zephyr/drivers/gpio.h>
#include <zephyr/logging/log.h>
#include <zephyr/kernel.h>
#include <zephyr/device.h>
#include <zephyr/devicetree.h>
#include <stdlib.h>

LOG_MODULE_REGISTER(shell_gpio_emul);

#define OUTPUT_PIN_NODE DT_ALIAS(solenoids)
#define GPIO0 DEVICE_DT_GET(DT_ALIAS(gpio0))

struct output_pin_info {
    bool is_valid; 
    const char *label;
    struct gpio_dt_spec spec;
};

#define GET_OUTPUT_PIN_INFO(node_id) \
    COND_CODE_1(DT_NODE_HAS_PROP(node_id, gpios), \
    ( \
        { \
            .is_valid = true, \
            .label = DT_PROP(node_id, label), \
            .spec = GPIO_DT_SPEC_GET(node_id, gpios), \
        } \
    ), \
    ( \
        { .is_valid = false } /* Dummy entry for gpio_emul */ \
    ) \
    )

static const struct output_pin_info output_pin_list[] = {
    DT_FOREACH_CHILD_SEP(OUTPUT_PIN_NODE, GET_OUTPUT_PIN_INFO, (,))
};

static int cmd_display_emul_gpio_pins(const struct shell *sh, size_t argc, char **argv) {
    ARG_UNUSED(argc);
    ARG_UNUSED(argv);

    shell_print(sh, "--- Emulation Status ---");
    shell_print(sh, "%-15s | %-10s | %-5s | %s", "Label", "GPIO Dev", "Pin", "Level");
    shell_print(sh, "--------------------------------------------------");

    for (size_t i = 0; i < ARRAY_SIZE(output_pin_list); i++) {
        const struct output_pin_info *sol = &output_pin_list[i];

        if (!sol->is_valid) {
            continue;
        }

        if (!device_is_ready(sol->spec.port)) {
            shell_error(sh, "Error: Device %s is not ready", sol->spec.port->name);
            continue;
        }

        int state = gpio_emul_output_get(sol->spec.port, sol->spec.pin);

        shell_print(sh, "%-15s | %-10s | %-5d | %s", 
                    sol->label, 
                    sol->spec.port->name, 
                    sol->spec.pin, 
                    (state ? "HIGH (1)" : "LOW (0)"));
    }

    return 0;
}

SHELL_CMD_REGISTER(getsol, NULL, "Display output pin emulation states", &cmd_display_emul_gpio_pins);


static int cmd_set_emul_gpio_pins(const struct shell *sh, size_t argc, char **argv) {
    shell_print(sh, "letsgoo");
    gpio_emul_input_set(GPIO0, atoi(argv[1]), atoi(argv[2]));
    return 0;
}

// SHELL_CMD_REGISTER(setsol, NULL, "bla", &cmd_display_emul_gpio_pins);
SHELL_CMD_ARG_REGISTER(setsol, NULL, "bla", &cmd_set_emul_gpio_pins, 3, 0);
#endif

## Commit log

2025-10-11 Added hardware and firmware folder
    [SIGURD-B_Cu.gbl, SIGURD-B_Mask.gbs, SIGURD-B_Paste.gbp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]
2025-10-30 pwm but it does not work
    [main.c]
2025-11-01 Fixed the rest of the cubeIDE code, ready to be implemented into Zephyr
    [main.c]
2025-11-02 some changes pwm still does not work
    [main.c]
2025-11-02 pwm test now works!!!
2025-11-02 servoZero and servoRotate works
2025-11-02 builds now; fixed variable not declared
    [main.c]
2025-11-12 Fáfnir V1.1 redesign
    [BOM-SIGURD.csv, Ignition.kicad_sch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]
2025-11-13 dummy CAN receiving but not tested on actual board
2025-11-24 fafnir redesign :)
    [BOM-SIGURD.csv, Ignition.kicad_sch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]
2026-03-02 native sim board file
